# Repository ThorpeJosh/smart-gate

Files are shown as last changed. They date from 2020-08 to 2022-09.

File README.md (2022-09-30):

# Raspberry pi powered smart gate
Build Status (https://jenkins.thorpe.engineering/job/smart_gate/job/master/) 
Deployment Status (https://jenkins.thorpe.work/job/smart-gate-deploy/)  
This repo is for an IOT inspired raspberry pi controller for a motorised gate.  
In this application the gate is driven by a 24V motor with a 24V battery and solar charging system. 
An internet connection is supplied to the Raspberry Pi (RPi) via ethernet, and in the initial application of this project the gate was in a remote location where a pair of long range wifi APs in a wireless bridge mode were used to give internet access to the RPi. 
This Internet connection supports features such as sending email alerts, deploying code updates remotely, and a simple API for remote control and receiving information from anywhere in the world.

Since the RPi has no analog pins, an Arduino UNO is used for all the analog inputs and sends the analog voltages over USB to the RPi upon request.
When an update is deployed the RPi will compile and upload the new arduino code to the Arduino via the USB.

This project was initially designed around a specific application, but could be easily forked and applied to different motorised gate applications or contributions to the project that help generalise it are welcome.

## Wiring
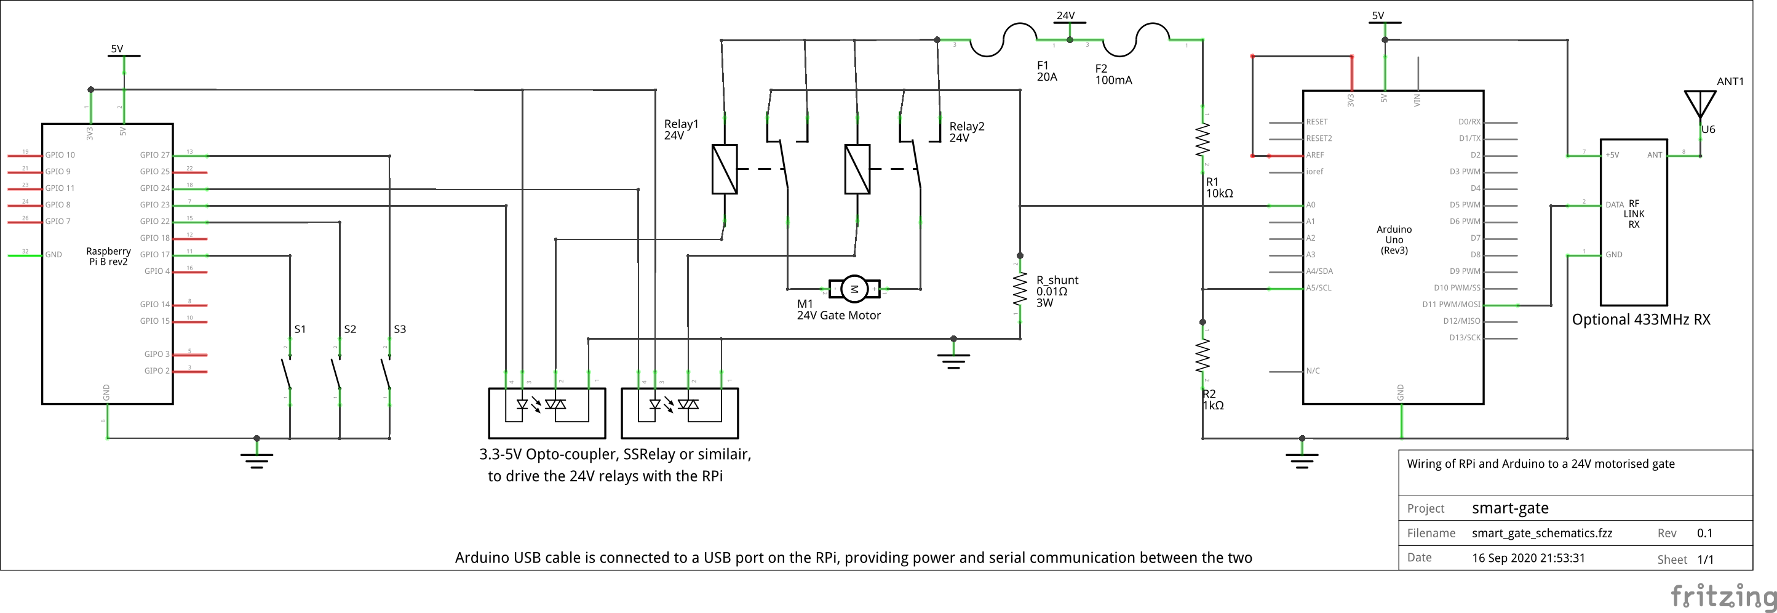
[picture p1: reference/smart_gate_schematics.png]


### RPi Inputs
* 3 push-buttons (Normally Open, Activating button grounds the pin)
  * Outside the property, activated when entering
  * Inside the property, activated when exiting
  * On the control box mounted on the gate post, used for debugging
* Arduino serial via USB
  * Voltage across a shunt to measure current through motor for hit detection
  * Battery voltage for logging and alerts

### RPi outputs
* Gate Motor (2 pins, driving SPDT relays in a H-bridge configuration)

### Arduino Inputs
* Analog input from all pins (RPi decides what pins to use/ignore)
* ASK 433MHz Receiver for radio operation of the gate (Optional)

## Modes
Gate has 3 modes it can operate in
  * Normal - Closed unless a button is pushed, then it opens for a set period of time then closes again.
    If the gate hits an object when opening, it will stop the motor and wait for another button push.
    If the gate hits an object when closing, it will re-open.
  * Away - Same as normal but sends email alert when button is pressed
  * Permanently Open - Gate opens and stays there until mode is changed
  * Permanently Closed - Gate closes and stays there until mode is changed

## Configuration
All the configurable values and parameters (such as pins used, tunables and secret keys) can be found in:
```bash
~/.config/smart-gate/conf.ini
```
This directory and conf.ini file will be created when the program is launched for the first time. Then change the default values as needed.
A sample of the conf.ini file is as follows:
```ini
[raspberry_pins]
# first pin of the motor
motor_pin_0 = 23
# second pin of the motor
motor_pin_1 = 24
# pin for the button on outside of the gate
button_outside = 27
# pin for the button on inside of the gate
button_inside = 22
# optional pin for debugging or mounted on control box
button_debug = 17

[arduino_pins]
# analog pin connected to the current shunt
shunt = 0
# analog pin connected to the 24vdc battery voltage divider
battery_voltage = 5

[parameters]
# minimum time to hold the gate open for, pushing a button when the gate is open will start this countdown again (seconds)
hold_open_time = 10
# expected time for gate to open/close, used to determine if something has gone wrong like hitting a car or a faulty motor (seconds)
expected_time_to_open_close = 23
# voltage threshold across shunt for the gate hitting an object (volts)
shunt_threshold = 0.03
# delay before reading shunt voltage, due to motor startup current spike (seconds)
shunt_read_delay = 0.5
# correction factor for battery voltage input. gets multiplied to the arduinos voltage reading on the battery voltage pin
battery_voltage_correction_factor = 10.7

[keys]
# secret key to use for 433mhz radio, if being used. must be 8 characters
radio_key = 8CharSec
```

## Email Alerts (Optional)
To enable email alerts, an email config must exist at ~/.config/smart-gate/email_keys.json following the following format:
```json
{
    "smtp": "gate_smpt_email_server",
    "port": 123,
    "fromaddr": "gate@email.example",
    "toaddrs": ["recipient1@email.example", "recipient1@email.example"],
    "subject": "GATE ALERT",
    "credentials": {
        "id": "gate@email.example",
        "key": "email_credentials"
    }
}
```

## 433MHz Radio Control (Optional)
The gate can be opened with cheap 433MHz radios when a receiver is fitted to the Arduino. See the wiring diagram for the how to wire the receiver, and code to program the transmitters can be found in arduino_src/TransmitterSketch/TransmitterSketch.ino

The 8 character secret for the Arduino to listen for, must be set in ~/.conf/smart-gate/conf.ini\
The RPi will automatically send this key to the Arduino when the serial handshake is completed.

## Termux UI (Android)
The gate can be controlled via ssh from any computer or mobile.\
For a simple alias based ui, see shell_ui/aliases, and consider appending this file to your bashrc.  

To install or update a Termux UI for android devices:
* Set your smart-gate RPi up with a static ip on a local network or vpn
* Dowload Termux app on your android, Info at [termux.com](https://termux.com/)
* Install open-ssh in Termux and setup ssh-keys with the RPi server
* Then run the following in a Termux shell substituting the ip address of the RPi smart-gate server.
```bash
export ip=192.168.0.5
curl -sS https://raw.githubusercontent.com/ThorpeJosh/smart-gate/master/shell_ui/install_ui_termux.sh | bash
```

## Deploying to a Raspberry Pi
Instructions for a Debian based OS like Raspbian/Raspberry Pi OS.
### Installation
Install python3 and virtualenv
```bash
sudo apt update && sudo apt install -y python3-dev virtualenv
```

Clone this repo in the pi users home directory
```bash
cd /home/pi
git clone https://github.com/ThorpeJosh/smart-gate.git
```

### Deployment
To deploy simply run
```bash
bash smart-gate/deploy.sh
```
This will setup a virtual environment and install all requirements.
It also adds a cronjob to the pi user to run the smart-gate program automatically.

## Working on this repository
Instructions for Debian based OS
### Installation
Install python3 and virtualenv
```bash
sudo apt update && sudo apt install -y python3-dev virtualenv
```

Create a python3 virtual environment
```bash
virtualenv venv -p python3
```

Activate the virtual environment
```bash
source venv/bin/activate
```

Install the python requirements
```bash
pip install .[dev]
```

### Usage
From a raspberry pi run
```bash
python src/main.py
```

### Pylint
To run the lint filter (Also done by Jenkins on any PRs)
```bash
pylnt src/*
```

### Pytest
To run the unit tests (Also done by Jenkins on any PRs)
```bash
pytest
```

## To-do list
### Phase 1
* Completed

### Phase 2
* Capture picture of vehicle when button is pressed
* Remove all busy waiting (Optimize to reduce cpu usage by removing while loops with delays)

### Phase 3
* Number Plate detection
* Vehicle/person detection

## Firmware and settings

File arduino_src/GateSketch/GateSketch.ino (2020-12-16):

// vim: filetype=cpp
/*Arduino code to communicate with the RPi over serial.
Information shared with RPi includes analog pin voltages and other inputs that trigger the gate.
All analog readings will be smoothed and converted to voltages (floats)

Serial communication contract as follows:

Handshake:
    Arduino sends 'A', RPi responds with 'A'
Button Pin Negotiation:
    Arduino sends 'B', RPi sends pin numbers as chars for each button pin, then 'B' when it's finished.
Analog Voltages:
    RPi sends 'V', Arduino responds with 'V' followed by voltages[] and then a checksum
Gate Trigger:
    Arduino sends 'O', followed by a trigger message, RPi doesn't respond.

*/
#include <SPI.h>
#include <QuickMedianLib.h>
#include <Servo.h>

// Configurable Parameters 
const int noOfAnalogPins = 6;
const int voltageDecimalPlaces = 4;
const int lengthOfRadioKey = 8; //Length of expected secret key to receive over 433MHz radio


// Globals
float voltages[noOfAnalogPins];
float checksum;
byte incomingByte;

// Servo
Servo servo;
byte servoPos;
const int servoPin = 9;

// Button pins are given by RPi, presume less than 10 buttons will be used
int buttonPins[10] = {0};
unsigned long lastButtonPress = 0;
unsigned long debounceDelay = 1000;


void setup()
{
    // Use external analog reference and put a jumper between pins 3.3V and AREF
    analogReference(EXTERNAL);
    servo.attach(servoPin);
    // start serial at 115200bps
    Serial.begin(115200);
    serialHandshake();
    // Get button pins and initialize them
    pinMode(LED_BUILTIN, OUTPUT);
    digitalWrite(LED_BUILTIN, LOW);
    getButtonPins();
    for (int i=0; i<10; i++)
    {
        if (buttonPins[i] > 0)
        {
            Serial.print("Initializing input, digital pin number: ");
            Serial.println(buttonPins[i]);
            pinMode(buttonPins[i], INPUT_PULLUP);
        }
    }
}


void loop()
{
    if (Serial.available() > 0)
    {
        incomingByte = Serial.read();
        if (incomingByte == 'V')
        {
            // Read analog pins and send data if requested over serial
            sendAnalogVoltages();
        }
        else if (incomingByte == 'S')
        {
            // RPi is sending a servo position update
            updateServo();
        }
    }
    // Check if buttons have been pressed
    if ((millis() - lastButtonPress) > debounceDelay)
    {
        if (checkButtons())
        {
            lastButtonPress = millis();
            //Toggle led
            digitalWrite(LED_BUILTIN, !digitalRead(LED_BUILTIN));
        }
    }
}

void flushSerialInputBuffer()
{
    while (Serial.available() > 0)
    {
        Serial.read();
    }
}

void updateServo()
{
    // Wait until we recieve new byte
    while (Serial.available() <= 0)
    {
        Serial.println("Waiting for servo position");
        delay(100);
    }
    servoPos = Serial.read();
    Serial.print("Sending servo to position: ");
    Serial.println(servoPos);

    servo.write(servoPos);
}

void sendAnalogVoltages()
{
    updateAnalogVoltages();
    Serial.println('V');
    for(int i=0; i<noOfAnalogPins; i++)
    {
        Serial.println(voltages[i], voltageDecimalPlaces);
    }
    Serial.println(checksum, voltageDecimalPlaces);
}

void updateAnalogVoltages()
{
    // Update the global voltages array
    
    // Take multiple readings and then apply median
    int noSamples = 21;
    int analogVals[noOfAnalogPins][noSamples];
    
    // Take samples over noSamples*delay() seconds
    for(int s=0; s<noSamples; s++)
    {
        for(int i=0; i<noOfAnalogPins; i++)
        {
            analogVals[i][s] = analogRead(i);
        }
        delay(1);
    }

    // Get median for each pin
    for(int i=0; i<noOfAnalogPins; i++)
    {
        voltages[i] = float(QuickMedian<int>::GetMedian(&analogVals[i][0], noSamples));
    }

    // Multiply by 3.3/1023 to get voltage
    for(int i=0; i<noOfAnalogPins; i++)
    {
        voltages[i] = (voltages[i]) * (3.3 / 1023.0);
    }

    // Calculate the checksum
    checksum = 0.0;
    for(int i=0; i<noOfAnalogPins; i++)
    {
        // Round the voltages to the correct decimal places
        checksum += round(voltages[i]*float(pow(10, voltageDecimalPlaces)))/float(pow(10, voltageDecimalPlaces));
    }
}

void serialHandshake()
{
    // Wait until we recieve a byte
    while (Serial.available() <= 0)
    {
        Serial.println('A');
        delay(200);
    }
    flushSerialInputBuffer();
}

void getButtonPins()
{
    // Send an 'B' to request the button pins
    flushSerialInputBuffer();
    Serial.println('B');
    bool finished_flag = false;
    int buttonNo = 0;
    char incomingChar;
    
    Serial.println("Getting button pins");
    while (buttonNo < 10)
    {
        // Wait for serial packets
        while (Serial.available() <= 0)
        {
            Serial.println("waiting for next pin char");
            delay(1000);
        }
        incomingChar = Serial.read();
        // Check if all pins have been received
        if (incomingChar == 'B')
        {
            Serial.println("Got all pins");
            break;
        }
        // Check if value is valid
        if (incomingChar < '1')
        {
            continue;
        }
        // Convert ascii Char to byte
        byte pinNo = incomingChar - '0';
        Serial.print("Got pin: ");
        Serial.println(pinNo);
        buttonPins[buttonNo] = int(pinNo);
        buttonNo++;
    }
}


bool checkButtons()
{
    bool pressed;
    int noSamples = 50;
    for (int i=0; i<10; i++)
    {
        if (buttonPins[i] > 0)
        {
            pressed = !digitalRead(buttonPins[i]);
            // Check to ensure that this wasn't a false positive
            if (pressed)
            {
                for (int j=0; j<noSamples; j++)
                {
                    if (digitalRead(buttonPins[i]))
                    {
                        // Button is no longer pressed, ignore initial press
                        pressed = false;
                        break;
                    }
                    delay(1);
                }
            }
            if (pressed)
            {
                // Button has been pressed, send capital "O"
                Serial.println("O");
                // Send the pin number to RPi
                Serial.println(buttonPins[i]);
                break;
            }
        }
    }
    return pressed;
}

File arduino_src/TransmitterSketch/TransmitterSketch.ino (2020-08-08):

// vim: filetype=cpp 
/* Arduino code to upload to a radio transmitter to remotely open the gate,
when it is within a certain proximity.
Proximity will depend on the quility of the 433MHz transmitter/ receiver pair and their voltages.

Make sure to replace the secret key below with one of your choice (8 characters) and set it for the RPi,
as described in the README */

#include <RH_ASK.h>
#include <SPI.h> // Not actually used but needed to compile

RH_ASK driver;

const char *secretKey = "8CharSec";

void setup()
{
    driver.init();
}

void loop()
{
    driver.send((uint8_t *)secretKey, strlen(secretKey));
    driver.waitPacketSent();
    delay(500);
}

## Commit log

2020-05-02 Added old arduino code
2020-05-04 Fixed up pylint issues
    [main.py]
2020-05-07 Testing ADC
2020-05-07 Warning if I2C isn't enabled
2020-05-07 Tuned ADC median filtering
2020-05-08 Fixed message bug and FIFO thread run-on
    [job_queue.py]
2020-05-09 Skipping test in jenkins
    [test_job_queue.py]
2020-05-12 Battery voltage correction factor
    [config.py]
2020-05-12 Shunt Calibration
2020-05-12 Kill currently running python program whilst deploying
2020-05-19 Added fake GPIO library for non-RaspberryPi dev
2020-05-20 Added button input callbacks
2020-05-20 Added button logging
2020-05-21 Add button detections to job queue
2020-05-22 Motor digital output control
2020-05-24 mode_change to allow users to change current gate operating mode added
2020-05-24 Changed pin numbering to BCM
2020-05-24 Added battery logging module
2020-05-24 Start battery logger in main
2020-05-24 Added battery log to config
2020-05-24 Setup battery pin
2020-05-24 added reset for hold timer on button push and reopen during close on button push
    [main.py]
2020-05-26 Change pin configuration
2020-05-27 Robust button trigger
2020-05-27 Disable internal pull-up resistor
2020-05-27 Fix for old versions of os.path.join()
    [config.py]
2020-05-27 Log battery every hour instead of minute
2020-05-27 Fix cpu usage issue
    [main.py]
2020-05-30 Removed old arduino code
2020-05-30 Battery logger cleaned and priority messaging added
2020-05-30 Battery logger cleaned even more
2020-05-30 Set battery log to seperate log from root
2020-05-30 Log warning and critical battery voltages to root logger
2020-05-30 Change battery voltage logging message formats
2020-06-01 Fix critical log bug
    [battery_voltage_log.py]
2020-06-01 Fixed pylint duplicate-code false positive
    [gate.py, main.py]
2020-06-01 Unit tests for adc
2020-06-01 Mock mode for non-RPi devices
2020-06-03 Change battery warning voltages
2020-06-06 Allow adc mock interface to run on RPi
2020-06-06 Changed default adc mock values to zero
2020-06-07 Cleanup/kill JobQueue threads properly
2020-06-11 Email logger for ERROR or above
    [main.py]
2020-06-15 Fix battery voltages and open time limit
    [battery_voltage_log.py, config.py]
2020-06-15 Fix logging in change_mode
    [gate.py]
2020-06-15 Email alerts on button press
2020-06-16 Adjust voltage log voltages
2020-06-17 Move button setup to gate module
2020-06-17 rotate battery log every week
2020-06-19 Add button objects to instance
2020-06-27 Revert "Add button objects to instance"
    This reverts commit e4c686a15ee4230a56fdd4538f81b8e6963c1d24.
    [gate.py]
2020-06-29 Arduino analog read sketch
2020-06-29 Arduino install compile verify and upload scripts
2020-06-29 Change adc module to serial module
2020-06-29 Add arduino cpp compilation to Jenkins
2020-06-29 Add arduino code upload to deploy process
2020-06-29 RPi Module to get analog readings from arduino
2020-06-29 Convert analog from adc to serial
2020-06-29 Make unit tests more robust to random failures
    [test_gate.py, test_main.py, test_serial_analog.py]
2020-06-29 Use 3.3v analog reference for greater accuracy
2020-06-30 Raise priviliges in deploy script for arduino-cli install
2020-06-30 Avoid opening delay when sending emails
    [gate.py]
2020-07-19 Add checksum to analog voltages
2020-07-22 Serial timeout
    Serial timeout
    Serial timeout
    Serial timeout
    Checksum bug fix
    [serial_analog.py]
2020-07-22 Fix serial init calls in main and gate.py
    [gate.py, main.py]
2020-07-22 Catch serial errors and kill main thread to force a restart
    [serial_analog.py, test_serial_analog.py]
2020-07-22 voltage queue reading timeout when serial fails
    [serial_analog.py]
2020-07-25 Catch arduino queue timeouts
2020-07-25 Allow battery voltage to be logged on request
2020-07-25 Tweak the battery voltage correction factor
    [battery_voltage_log.py, config.py, job_queue.py]
2020-08-07 Receive 433MHz radio messages on Arduino
2020-08-07 Remove pi user requirement to install arduino-cli
2020-08-07 RPi to open gate upon Arduino's request
2020-08-07 Read secret radio key and give to Arduino
2020-09-16 Created schematics
    [smart_gate_schematics.fzz]
2020-09-16 Add schematic diagram to README
2020-11-11 Fix button callback test bug
    [test_gate.py]
2020-11-11 Raise error if mode is incorrectly set
    [main.py]
2020-11-11 Add debug logs and current mode to shell UI
2020-11-11 Start serial reading thread after handshake
2020-11-12 Add RPI pin factory to requirements
2020-11-12 Arduino handle buttons
2020-11-16 Arduino read button state and report to RPi
2020-11-16 Log all arduino messages to file
2020-11-16 Remove RPi button handling
2020-11-16 Allow Arduino to trigger button press
2020-11-16 Change buttons to arduino in conf.ini
2020-11-16 remove button setup test
2020-11-16 Send button pins to Arduino when requested
2020-11-17 Remove test using old RPi buttons
2020-11-17 Swap button pins
2020-11-18 Median filtering on all analog inputs
2020-11-18 Robust button pressing
2020-11-18 Change arduino log level to debug
2020-11-18 Add battery alert voltages to conf.ini
2020-11-18 Allow alert voltages to be changed from conf
2020-11-19 Arduino servo handling
2020-11-19 Add camera readthedocs requirement
2020-11-19 Write camera parameters to conf.ini
2020-11-19 Setup global camera parameters
2020-11-19 Add camera queue and servo control to camera class
2020-11-19 Verify servo angles in conf.ini are valid
2020-11-19 Add Servo library to arduino requirements
2020-11-19 Remove arduino radio due to conflict with servo
2020-11-19 Trigger camera when button is pushed
2020-11-19 Add camera debug messages
2020-11-19 Change default servo angle to safer values
2020-12-16 Reduce robust sampling as it required button to be held
2021-03-04 arduino-cli changed default compile behaviour to include --dry-run
2021-04-04 Add db entry when button pushed
2021-04-04 Skip email_handler init when no email config supplied
    [config.py]
2021-04-06 Add battery logging to db
2021-04-06 Add try deploy db message to connection error
    [db.py]
2022-10-25 Give container access to system devices
2022-10-26 cicd: matrix pipeline for all arm architectures
2022-10-26 cicd: print architecture at each stage
2022-10-26 cicd: allow dockerfile builds of arm and x86
2022-11-07 cicd: cleanup Dockerfile and insert env variables
